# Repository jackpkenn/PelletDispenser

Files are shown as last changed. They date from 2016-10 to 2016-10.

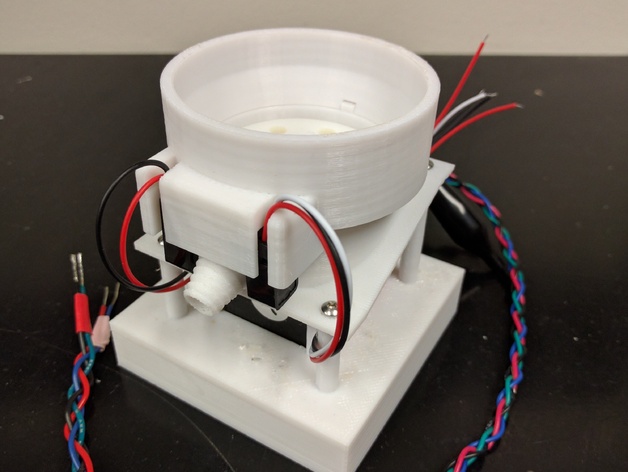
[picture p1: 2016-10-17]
Completed Feeder Preview 2.jpg

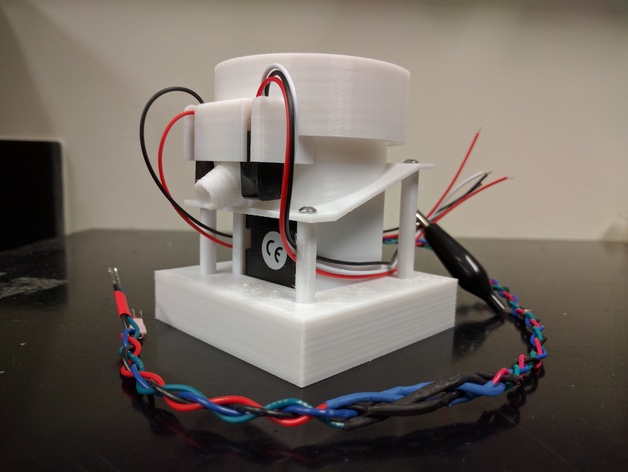
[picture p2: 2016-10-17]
Completed Feeder Preview 1.jpg

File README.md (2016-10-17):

# Pellet Dispenser

This food pellet dispenser was developed by Dylan Guenther and Jack Kennedy at Dr. Andrew Maurer's Lab in the McKnight Brain Institute at the University of Florida. The dispenser consists of four separate 3D printed components and uses a bipolar stepper motor to dispense individual 45mg food pellets. An infrared break-beam attached to one of the external interrupt pins is used to keep track of how many pellets have been dispensed. The dispenser is designed to be operated with an Arduino using an Adafruit motor driver shield and can be adapted to any other micro-controller and H-bridge.

## Parts List
* __4x - M3x0.5 hex nut__ (McMaster-Carr part number: [90695A033](http://www.mcmaster.com/#90695A033))
* __2x - M3 35mm socket cap screw__ (McMaster-Carr part number: [92095A201](http://www.mcmaster.com/#92095A201))
* __2x - M3 50mm socket cap screw__ (McMaster-Carr part number: [92095A475](http://www.mcmaster.com/#92095A475))
* __1x - 3mm IR break-beam__ (Adafruit part number: [2167](https://www.adafruit.com/product/2167))
* __1x - Adafruit Motor Shield v2__ (Adafruit part number: [1438](https://www.adafruit.com/product/1438))
* __1x - Nema 14 bipolar stepper motor__ (Pololu part number: [1208](https://www.pololu.com/product/1208))
* __1x - Arduino Uno R3__ (Adafruit part number: [50](https://www.adafruit.com/products/50))

## Code Examples
Break-beams are interrupt driven to keep track of the number of pellets dispensed. The Adafruit motor driver library was used to handle the motor control.
```cpp
void beamBroken_isr(){
  noInterrupts();
  pells--;
  disp++;
  broken = true;
  Serial.println("Beam Broken");
  if(disp == 5){
    disp = 0;
    rot = !rot;
  }
  interrupts();
}
```
The dispenser is set to switch the direction of the rotor after every five steps. This was found to reduce jamming and crushed pellets. A delay of 100ms was added after each step to help the break-beams to detect individual pellets.
```cpp
if (f == "disp" || f == "Disp") {
  pellsR = param;
  Serial.print("Dispensing ");
  Serial.print(param);
  Serial.println(" pellets");
  while(pells>0){
    if(rot == false){
      myMotor->step(25, FORWARD, SINGLE);
      delay(100);
    }
    else if(rot == true){
      myMotor->step(25, BACKWARD, SINGLE);
      delay(100);
    }
  }
}
```
## License and Disclaimer
This software is open-sourced under the MIT Licence (see ```LICENSE``` for the full license).

The software is provided as is. It might work as expected - or not. Just don't blame us.

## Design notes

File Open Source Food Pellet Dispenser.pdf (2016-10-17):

## Open Source Food Pellet Dispenser

v1.0

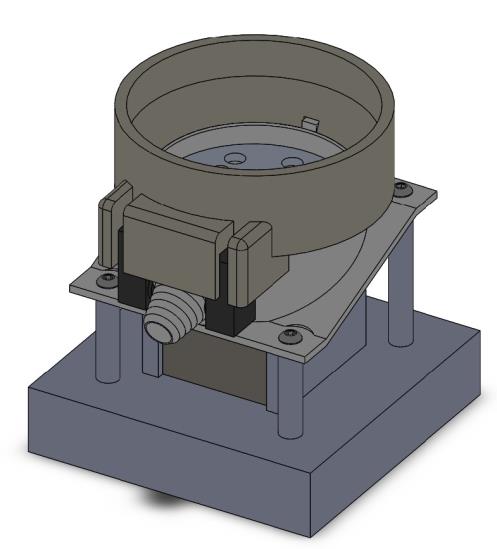
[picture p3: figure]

Summary

This food pellet dispenser was developed by Dr. Andrew Maurer's Lab in the McKnight Brain Institute at the University of Florida. The dispenser consists of four separate 3D printed components and uses a bipolar stepper motor to dispense individual 45mg food pellets. An infrared break-beam attached to one of the external interrupt pins is used to keep track of how many pellets have been dispensed. The dispenser is designed to be operated with an Arduino using an Adafruit motor driver shield and can be adapted to any other micro-controller and H-bridge.

Part List

Description | Quantity | Supplier | Part Number
M3x0.5 Hex Nut | 4 | McMaster-Carr | 90695A033
M3 35mm Socket Cap Screw | 2 | McMaster-Carr | 92095A201
M3 50mm Socket Cap Screw | 2 | McMaster-Carr | 92095A475
3mm IR Break-beam | 1 | Adafruit | 2167
Nema 14 Bipolar Stepper | 1 | Pololu | 1208

The feeder consists of four separate 3D printed components:

1) Motor Base – Designed to house a Nema 14 stepper motor
2) Dispenser Body

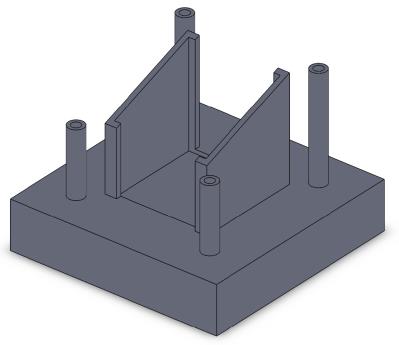
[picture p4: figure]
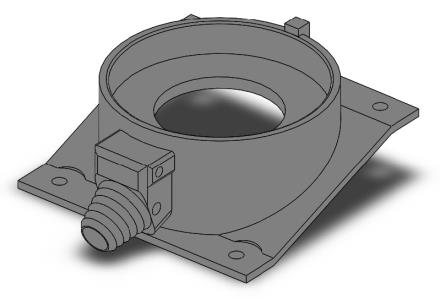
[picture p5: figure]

3) Rotor – Bottom view shows the slotted shaft hole

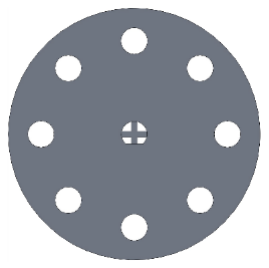
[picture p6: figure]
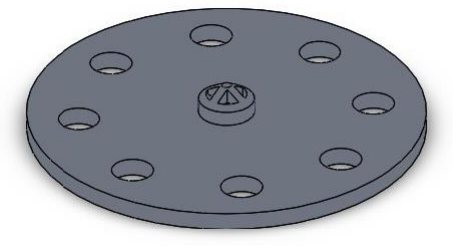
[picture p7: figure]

4) Feeder Cap – Holds break-beams in place with cutouts for wires

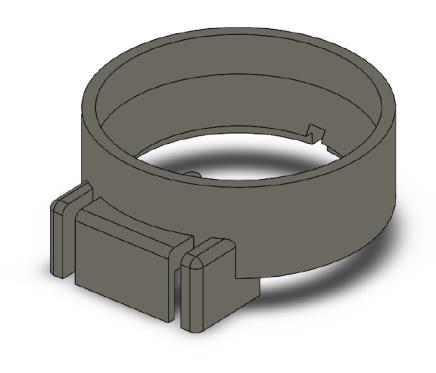
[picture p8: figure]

Code Examples

Break-beams are interrupt driven to keep track of the number of pellets dispensed. The Adafruit motor driver library was used to handle the motor control.

void beamBroken_isr(){
noInterrupts();
pells--;
disp++;
broken = true;
Serial.println("Beam Broken"); if(disp == 5){
disp = 0;
rot = !rot;
}
interrupts();
}

The dispenser is set to switch the direction of the rotor after every five steps. This was found to reduce jamming and crushed pellets. A delay of 100ms was added after each step to help the break-beams to detect individual pellets.

if (f == "disp" || f == "Disp") {
pellsR = param;
Serial.print("Dispensing "); Serial.print(param);
Serial.println(" pellets");
while(pells>0){
if(rot == false){
myMotor->step(25, FORWARD, SINGLE); delay(100);
}
else if(rot == true){
myMotor->step(25, BACKWARD, SINGLE); delay(100);
}
}
}

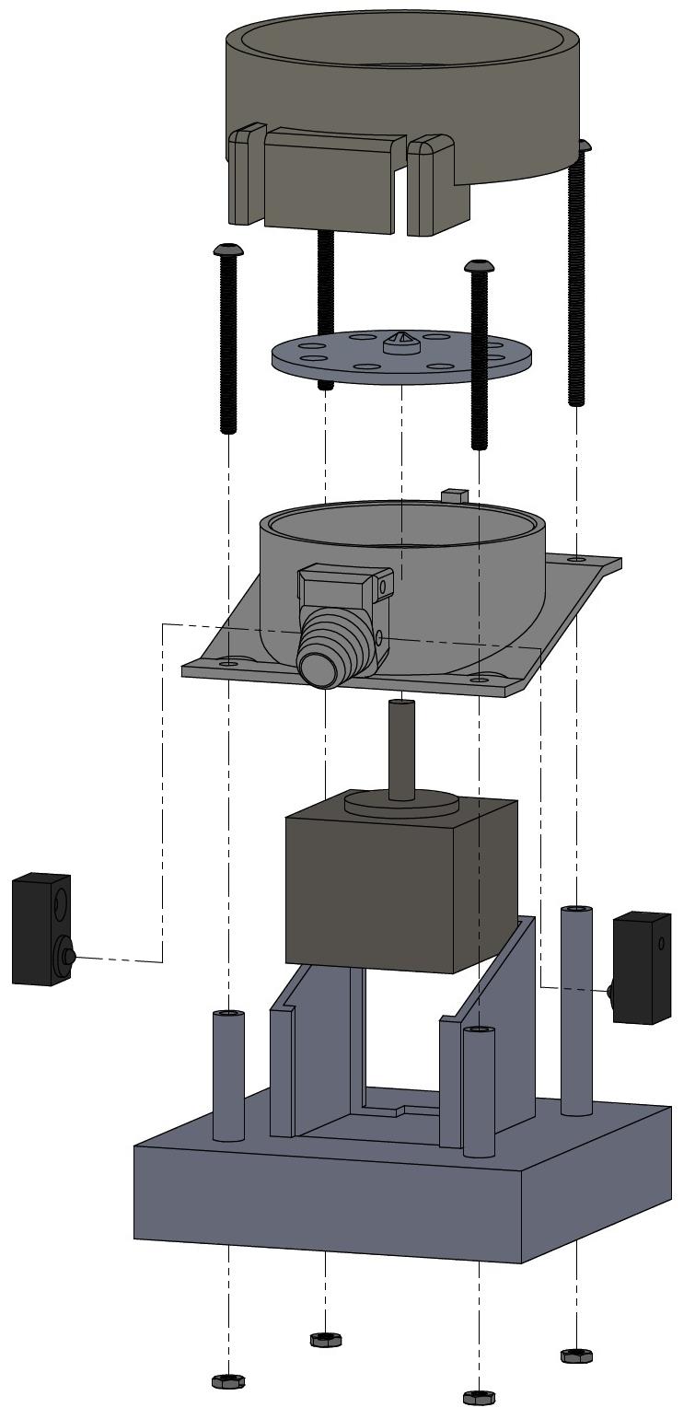
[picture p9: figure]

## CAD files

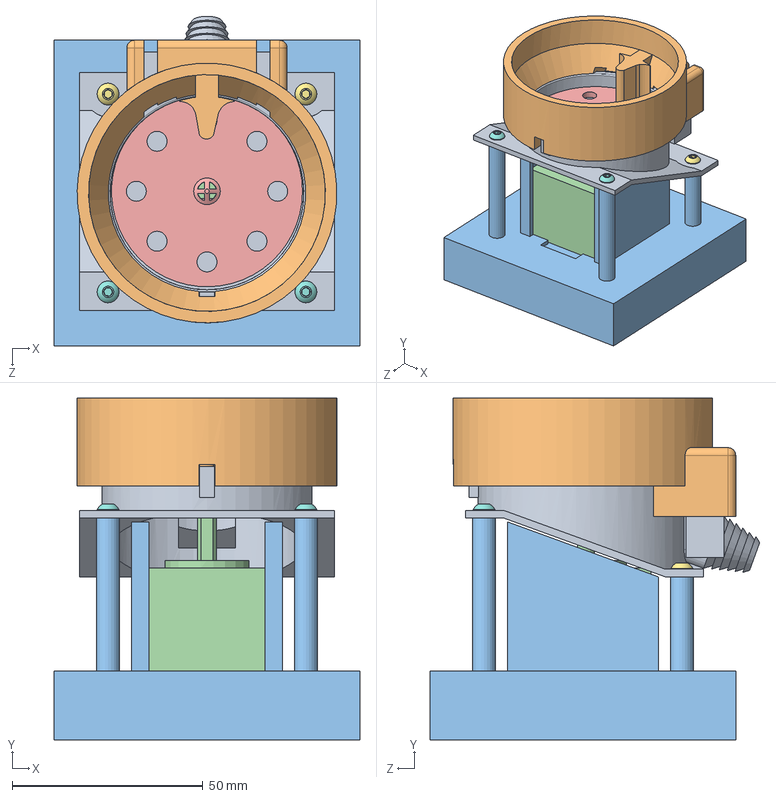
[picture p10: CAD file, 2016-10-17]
SOLIDWORKS-Part-Files/FinalFeeder.SLDASM
80.0 x 89.5 x 86.3 mm
Base V7
Lid V5
Motor Base V3
MotorModel
Rotor V10
90695A033 (Nut M3 thread) x 4
92095A201 (35mm lg M3 thread) x 2
92095A475 (50mm lg M3 thread) x 2
BreakBeam x 2

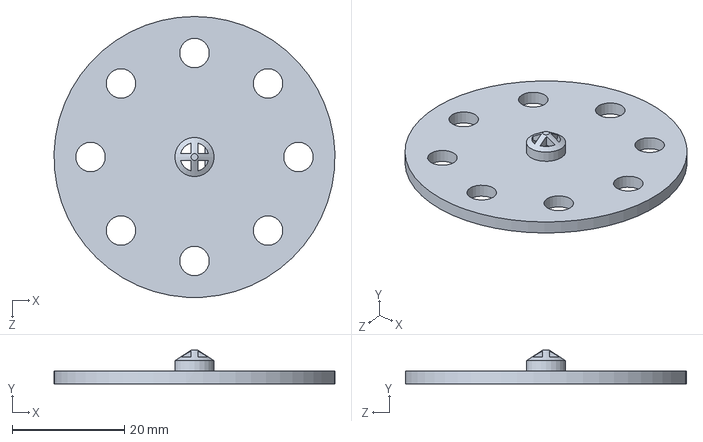
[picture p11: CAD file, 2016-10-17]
SOLIDWORKS-Part-Files/Rotor V10.SLDPRT
50.0 x 6.00 x 50.0 mm

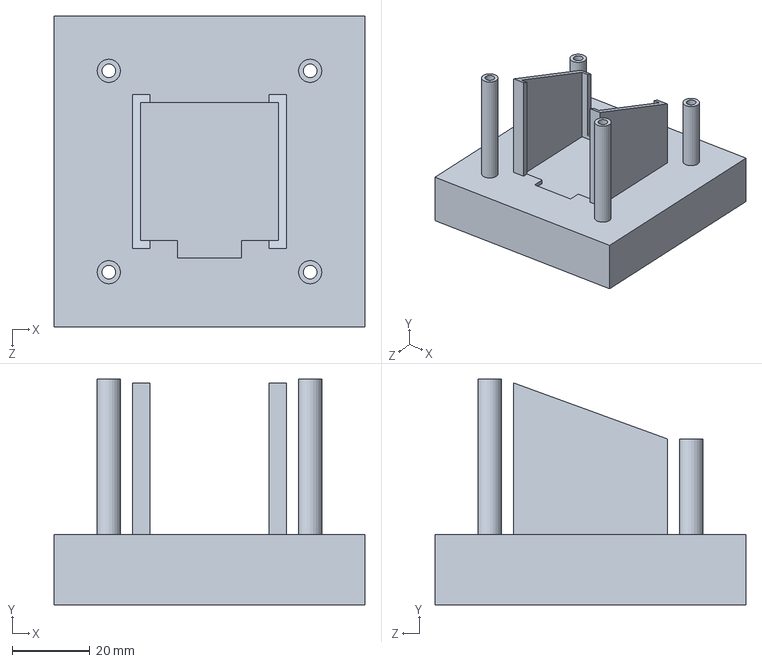
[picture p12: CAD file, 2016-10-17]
SOLIDWORKS-Part-Files/Motor Base V3.SLDPRT
80.0 x 58.1 x 80.0 mm

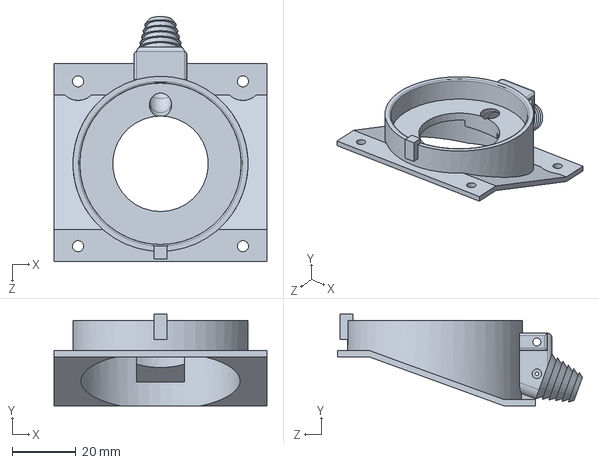
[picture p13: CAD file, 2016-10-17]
SOLIDWORKS-Part-Files/Base V7.SLDPRT
66.8 x 28.8 x 77.0 mm

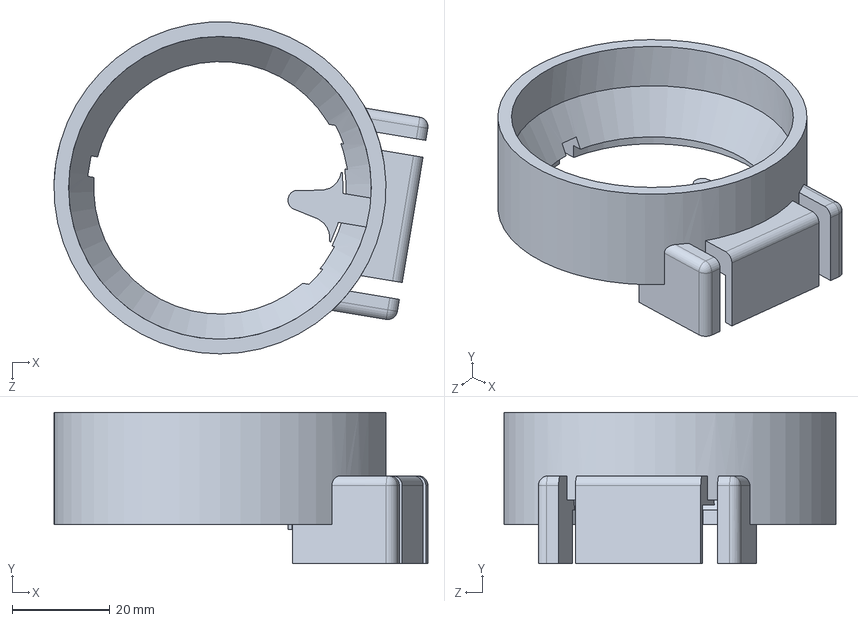
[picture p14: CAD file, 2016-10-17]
SOLIDWORKS-Part-Files/Lid V5.SLDPRT
76.6 x 31.0 x 67.9 mm

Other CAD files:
STL-Files/Base V7.STL
STL-Files/Lid V5.STL
STL-Files/Motor Base V3.STL
STL-Files/Rotor V10.STL

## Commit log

2016-10-17 Added STL and SOLIDWORKS part files
2016-10-17 Create STL file directory
2016-10-17 Added SOLIDWORKS part files
    [Base V7.SLDPRT, FinalFeeder.SLDASM, Lid V5.SLDPRT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]
2016-10-17 Added STL part files
    [Base V7.STL, Lid V5.STL, Motor Base V3.STL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]
